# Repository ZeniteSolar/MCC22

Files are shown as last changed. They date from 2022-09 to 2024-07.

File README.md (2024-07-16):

# MCC22

## Build
```bash
cd firmware
make -j16 -f STM32Make.make
```

MPPT Battery charger

| Input Voltage | 0 ~ 30 V  |
| ---: | :--- |
| Output Voltage  | 21 ~ 60V  |
| Output Power | 300 W |
| Efficiency | > 90% |

## 3D Model

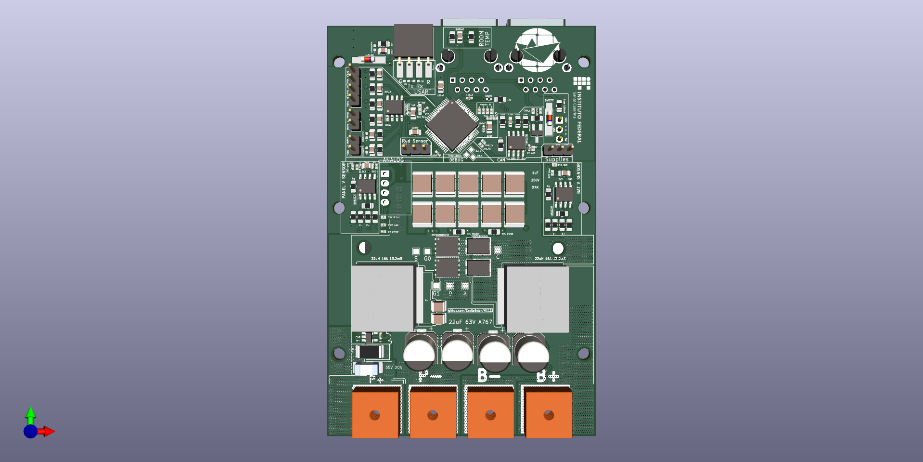
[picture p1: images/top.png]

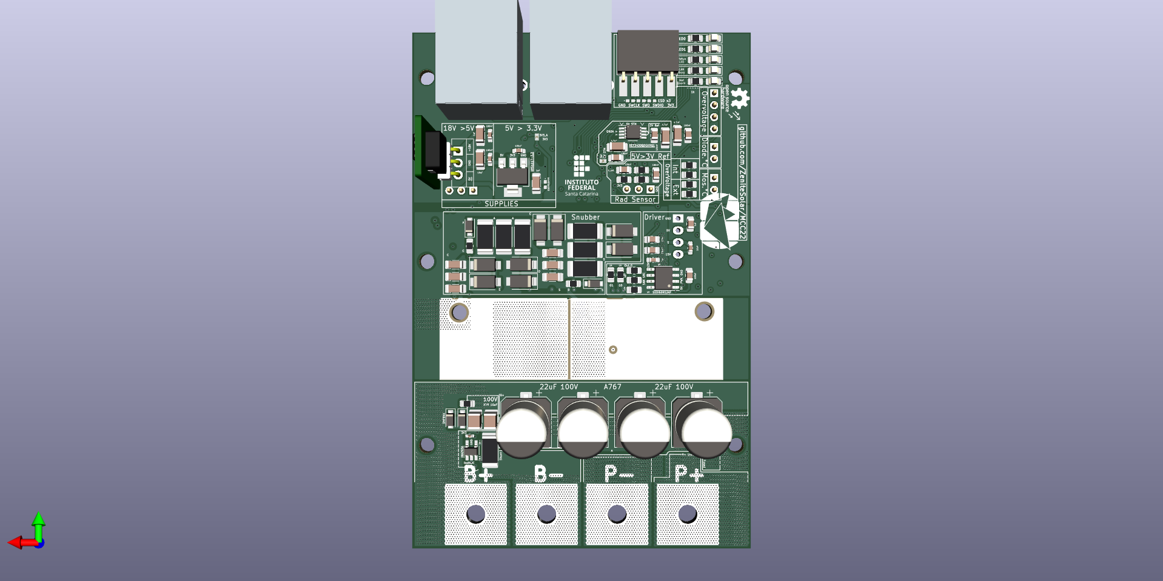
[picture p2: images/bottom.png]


## Soldered board

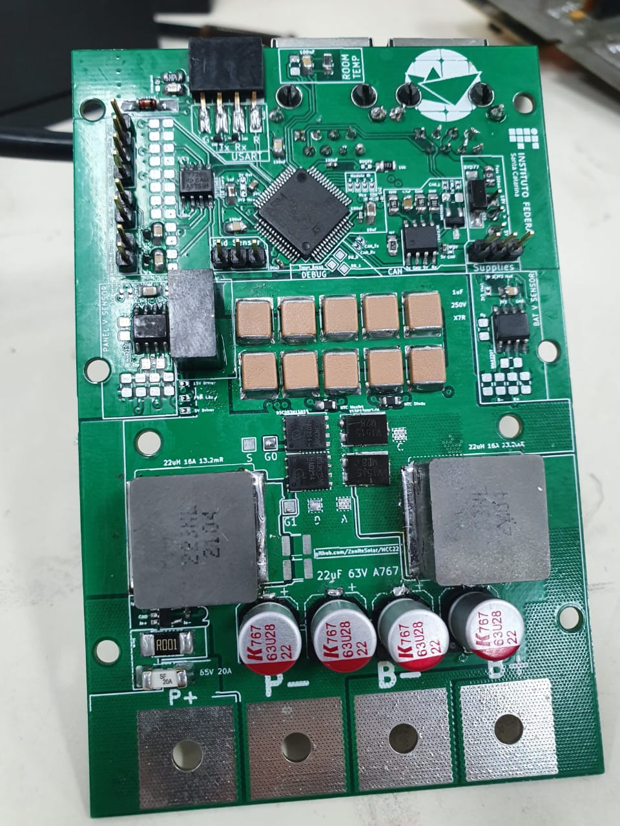
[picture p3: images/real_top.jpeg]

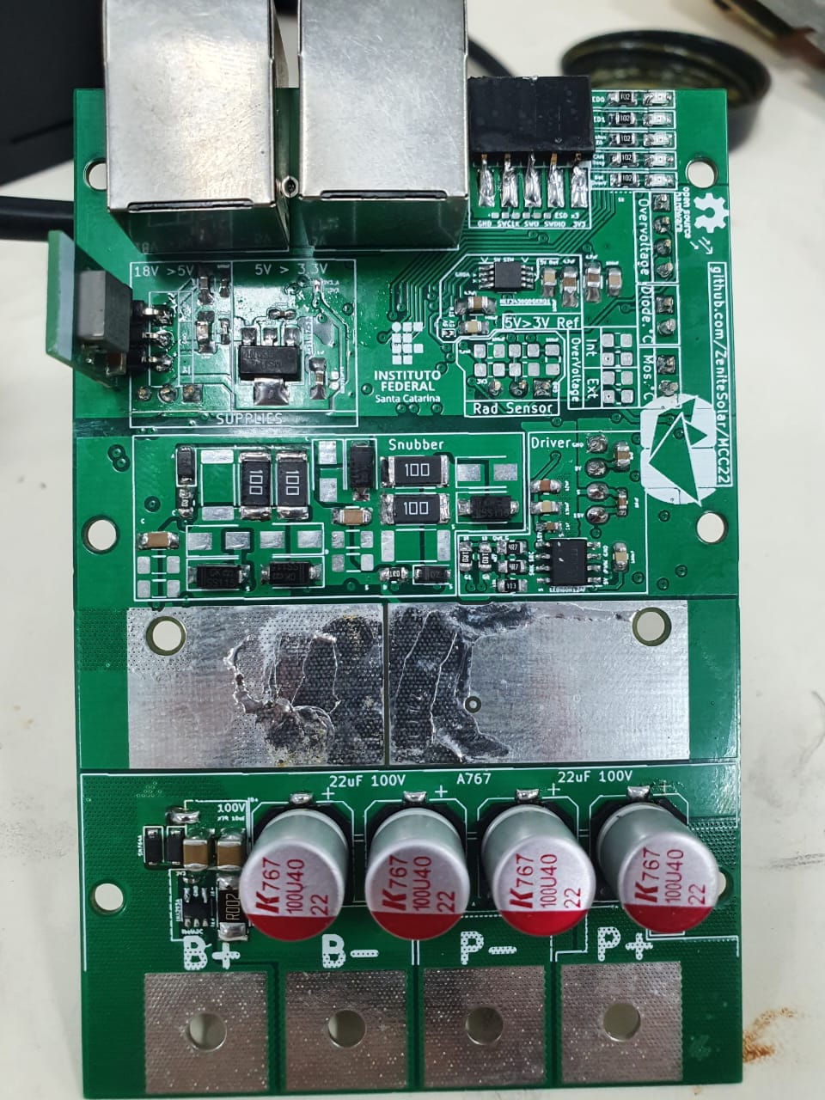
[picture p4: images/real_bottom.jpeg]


# Testing Guide for the MCC22 Board

Follow the steps below, if any value differs from the expected, abort the test. Power off and on after each step. Always limit the power source to 18V at 100mA. Use this [link](https://htmlpreview.github.io/?https://github.com/ZeniteSolar/MCC22/blob/main/hardware/main/bom/ibom.html) to find components on the board.

## Steps

1. Without any jumpers, connect the CAN with 18V, consumption should be approximately 1mA. On the power pin header (J601) there should be 5V and 3.3V at their respective pins.
2. Connect the STM 3.3V Enable jumper (JP101), consumption should be approximately 1mA.
3. Connect the STM32 Supply Enable jumper (JP201), consumption should be approximately 5mA. There should be 3.3V between the pins of capacitors C208 and C210.
4. Connect the STM 5V Enable jumper (JP103), consumption should be approximately 5mA. There should be 3V across the pins of capacitor C204.
5. Connect the Analog_Ref jumper (JP203) between the central pin and 3V_ref, consumption should be approximately 30mA. There should be 3V across the pins of capacitor C211.
6. Flash the STM32 (power should be on). When power is cycled, all LEDs should light up in sequence, excluding the Bat OverV LED. There should be a PWM signal on pin 1 of the PWM Enable jumper (JP106).
7. Connect the Enable_Analog jumper (JP102), the consumption should be approximately 5mA.
8. Connect a serial-USB converter and send the command `WRTE:SYST:PING?` to verify if UART is functioning, the response should be `PONG`.
9. Send the command `READ:MEAS:ALLM?`. After activating this flag, the board will continuously send the measurements it takes.
10. Connect a 10 Ohm resistor at the controller's output.
11. Send the command `WRTE:CTRL:ALGO:FIXD:0000.0000` to deactivate the PWM.
12. Connect the Disable_Vpanel jumper (JP301), the consumption should remain close to 5mA.
13. Connect the Disable_Vbat jumper (JP302), the consumption should remain close to 5mA.
14. Connect the Disable_Ibat jumper (JP304), the consumption should remain close to 5mA.
15. Connect the Disable_Ipanel jumper (JP303), the consumption should remain close to 5mA.
16. Connect a voltage source at P+ and P- with zero voltage and current at 10mA, increase the voltage to 30V and the VPan value on UART should follow the source voltage.
17. Connect a voltage source at B+ and B- with zero voltage and current at 10mA, increase the voltage to 60V and the Vbat value on UART should follow the source voltage.
18. Connect the Enable_Driver jumper (JP104) and consumption should be approximately 10mA. There should be 15V between pins 3 and 4 of the driver source (PS501).
19. Connect the Enable_Driver_5V jumper (JP502), Enable_Driver jumper (JP501), and Enable_PWM jumper (JP106), and the consumption should be approximately 12mA.
20. Send the command `WRTE:CTRL:ALGO:FIXD:0000.6000` to fix the PWM at 60%. Attach the oscilloscope's GND to test point S (TP404) **Other channels should have their GND disconnected!** and channel 1 to test point G0 (TP401). There should appear a square signal with a 60% duty cycle, same for G1 (TP402).
21. Connect a 10 Ohm load at the controller's output. Send the command `WRTE:CTRL:ALGO:FIXD:0000.6000`, connect a voltage source at P+ and P- with zero voltage and current at 1A, increase the voltage until the source limits and the Ipan value on UART should follow the source current.

Note: If any of the conditions are not met, there might be a potential issue with the board.

## Tests

All tests are in [this](./tests/tests.md) separated document.

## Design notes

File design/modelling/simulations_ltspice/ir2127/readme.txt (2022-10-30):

##########################################################################################
## Simulation model of IR2127 Level 1 for SIMetrix version 8.3g or higher
##########################################################################################

--------------------------------------------------------------------------------
1. Changelog
--------------------------------------------------------------------------------
VER    | BY                       | DATE          | OBS                         
--------------------------------------------------------------------------------
01.00  | GI                       | 2020-04-30    | created    (*1)
--------------------------------------------------------------------------------
01.01  | GI                       | 2020-12-02    | model update
--------------------------------------------------------------------------------
01.02  | GI                       | 2020-12-03    | model update
--------------------------------------------------------------------------------
01.03  | GI                       | 2020-12-04    | model update
--------------------------------------------------------------------------------

(*1) 
Simulation model of IR2127 Level 1 for SIMetrix version 8.3g or higher
Template performance : 
  - Static Electrical Characteristics and Dynamic Electrical Characteristics 
    are modeled with the typical values from the datasheet.
  - Temperature effects are not modeled
The following features have been modeled :
  - Switching Characteristics such as propagation delay, peak/mean currents
  - Undervoltage lockout 

--------------------------------------------------------------------------------
2. Supported platform
--------------------------------------------------------------------------------
This model has been successfully tested with the following software:
- SIMetrix 8.3g or newer versions

--------------------------------------------------------------------------------
3. Structure of the delivery package
--------------------------------------------------------------------------------
The delivery package contains the following:

	\Documentation\GettingStarted.pdf         : guidance on how to get started with the attached behavioral model
	\Documentation\Disclaimer.pdf             : Infineon’s model terms of use
	\Model\IR2127.lib                         : model lib file
	\Model\IR2127.sxslb                       : schematic symbol for the lib
	\Model\DEMO_TESTBENCH.sxsch               : demo testbench provided together with the model 
	\Model\IGBT_650V_TRENCHSTOP5_F5_L1.lib    : Infineon's IGBT model
	\Model\IGBT_650V_TRENCHSTOP5_F5_L1.sxslb  : Infineon's IGBT symbol for schematic
	\Model\results                            : some screenshots with the demo testbench and results
	
--------------------------------------------------------------------------------
4. Infineon contact and support
--------------------------------------------------------------------------------
support@infineon.com

--------------------------------------------------------------------------------
5. Disclaimer
--------------------------------------------------------------------------------

INFINEON’S MODEL TERMS OF USE

BY DOWNLOADING AND/OR USING THIS INFINEON MODEL (“MODEL”), THE USER (INCLUDING YOU) 
AGREES TO BE BOUND BY THE TERMS OF USE HERE STATED. IF USER DOES NOT AGREE TO ALL TERMS OF
USE HERE STATED, USER SHALL NOT DOWNLOAD, USE OR COPY THE MODEL BUT IMMEDIATELY DELETE 
IT (TO THE EXTENT THAT IT WAS DOWNLOADED ALREADY).

1. SCOPE OF USE
1.1 Any use of this Model provided by Infineon Technologies AG is subject to these Terms of Use.
1.2 This Model, provided by Infineon, does not fully represent all of the specifications and
operating characteristics of the product to which this Model relates.
1.3 This Model only describes the characteristics of a typical product. In all cases, the current data
sheet information for a given product is the final design guideline and the only actual 
performance specification. Although this Model can be a useful tool to evaluate the product 
performance, it cannot simulate the exact product performance under all conditions and it is 
also not intended to replace bread-boarding for final verification.

2. IMPORTANT NOTICE
2.1 Infineon Technologies AG (“Infineon”) is not and cannot be aware of the specific application of 
the Infineon’s Model by User. However, Model may from time to time be used by User in potentially 
harmful and/or life-endangering applications such as traffic, logistic, medical, nuclear or military a
pplications or in other applications where failure of the Model may predictably cause damage to 
persons’ life or health or to property (hereinafter "Critical Applications").
2.2 User acknowledges that Infineon has not specifically designed or qualified the Model for 
Critical Applications that the Model may contain errors and bugs and that User is required to 
qualify the Model for Critical Applications pursuant to the applicable local quality, safety and 
legal requirements before permitting or giving access to any such use.

3. CONFIDENTIAL INFORMATION
User shall treat ideas, concepts and information incorporated in the Model, the documentation and 
the content of this Terms of Use (together hereinafter "Confidential Information") confidential, not 
disclose it to any third party unless otherwise agreed in writing between User and Infineon, not use 
it for any other purposes than using the Model for simulation and testing purposes only.

4. WARRANTY
4.1 User acknowledges that the Model is provided by Infineon under this Terms of Use is provided free 
of charge and "AS IS" without any warranty or liability of any kind and Infineon hereby expressly 
disclaims any warranties or representations, whether express, implied, statutory or otherwise, 
including but not limited to warranties of workmanship, merchantability, fitness for a particular 
purpose, defects in the Model, or non-infringement of third parties intellectual property rights.
4.2 Infineon reserves the right to make corrections, deletions, modifications, enhancements, 
improvements and other changes to the Model at any time or to move or discontinue any Model without notice.

5. LIABILITY
5.1 Nothing in this Terms of Use shall limit or exclude Infineon's liability under mandatory liability 
laws, for injuries to life, body or health, for fraudulent concealment of defects in the software, or 
in cases of Infineon's intentional misconduct or gross negligence.
5.2 Without prejudice to Sections 5.1, in cases of Infineon's slight negligent breach of obligations 
that restrict essential rights or duties arising from the nature of this Terms of Use in a way that 
there is a risk of non-achievement of the purpose of this Terms of Use or of an obligation whose observance
User regularly may trust in and whereas compliance with only makes proper execution of this Terms 
of Use possible, Infineon's liability shall be limited to the typically, foreseeable damage.
5.3 Without prejudice to Sections 8.1 and 8.2, Infineon's liability under this Agreement shall be excluded in all 
other cases.

6. EXPORT REGULATIONS
The User shall comply with all applicable national and international laws and regulations, in 
particular the applicable export control regulations and sanction programs. The User also agrees 
not to export, re-export or transfer any software or technology developed with or using information, 
software or technology offered by Infineon, in violation of any applicable laws or regulations of 
the competent authorities. Further, the User shall neither use any products, information, software 
and technology offered by Infineon in or in connection with nuclear technology or weapons of mass 
destruction (nuclear, biological or chemical) and carriers thereof nor supply military consignees.

7. TERMINATION OF USE PERMIT
If the User violates these Terms of Use, such User’s permit to use this Model terminates automatically. 
In addition, Infineon may terminate the User’s permit to use this Model at its discretion and at 
any time regardless of any violation of these Terms of Use. In any of the foregoing events, the User 
is obliged to immediately destroy any content that has been downloaded or printed from Infineon’s website.

8. MISCELLANEOUS
8.1 These Terms of Use are subject to the laws of the Federal Republic of Germany with the exception 
of the United Nations on Purchase Contracts on the International Sale of Goods dated April 11, 1980 (CISG). 
The exclusive place of jurisdiction is Munich, Germany.
8.2 Should any provision in these Terms of Use be or become invalid, the validity of all other 
provisions or agreements shall remain unaffected thereby.

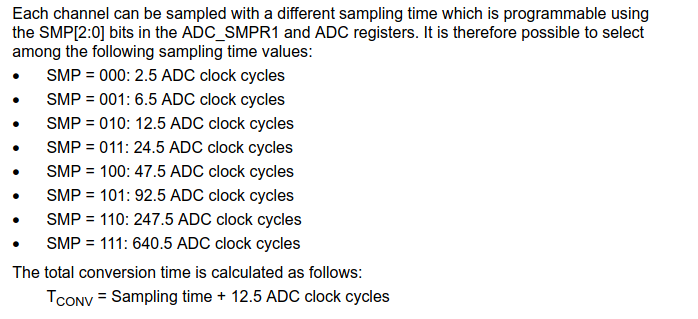
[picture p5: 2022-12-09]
design/img/Tsampl.png

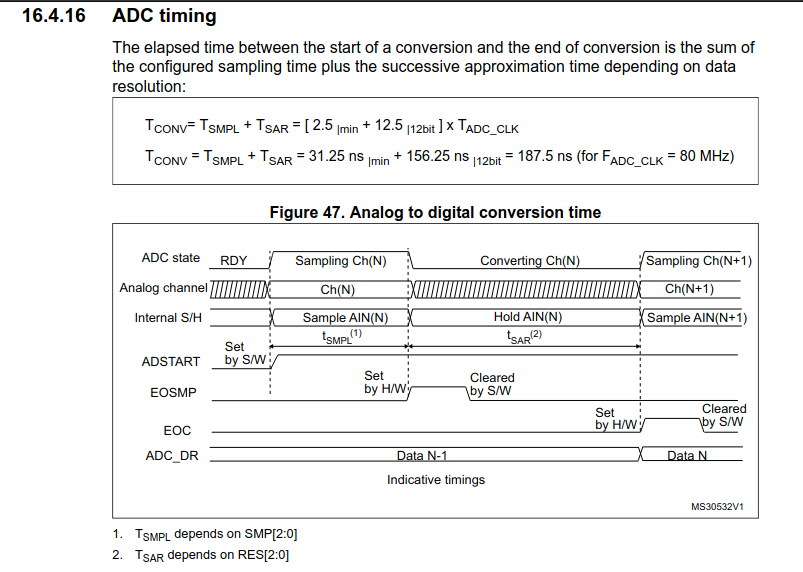
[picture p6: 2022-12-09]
design/img/ADC timing.png

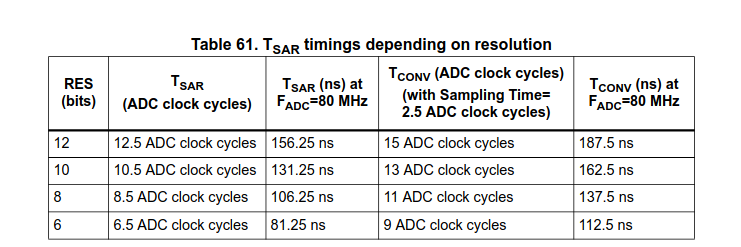
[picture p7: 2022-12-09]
design/img/Tsar.png

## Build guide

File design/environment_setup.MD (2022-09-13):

# Setting up the environment

### 1. Virtual Environment

```bash
python3.10 -m venv .venv
source .venv/bin/activate
python -m pip --upgrade pip
```

### 2. Project requirements
```bash
python -m pip install -r requirements.txt
```

Open `tllocalmgr` and:
```bash
install circuitikz
exit
```

and then:
```bash
sudo texhash
```

### 3.

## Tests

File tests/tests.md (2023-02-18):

### 1 Initial Test
The initial test of the system revealed that the inductor current was operating in a discontinuous mode, which resulted in poor efficiency and a significant amount of heat being generated in both the inductor and switches. After further analysis, two primary factors were identified.
- The first factor is the high ripple current in the inductor, which is causing increased core losses. 
- The second factor is the overly aggressive snubber, which is causing switching delays and high power dissipation in the snubber.

To explore the effects of different parameters on the system's performance, two tests were conducted using different switching frequencies of 40kHz and 100kHz. The duty cycle and load were varied to maintain a constant output voltage of 60V and input current levels of 3A and 6A. These tests were designed to identify the impact of these parameters on the system's efficiency, thermal behavior, and overall performance.

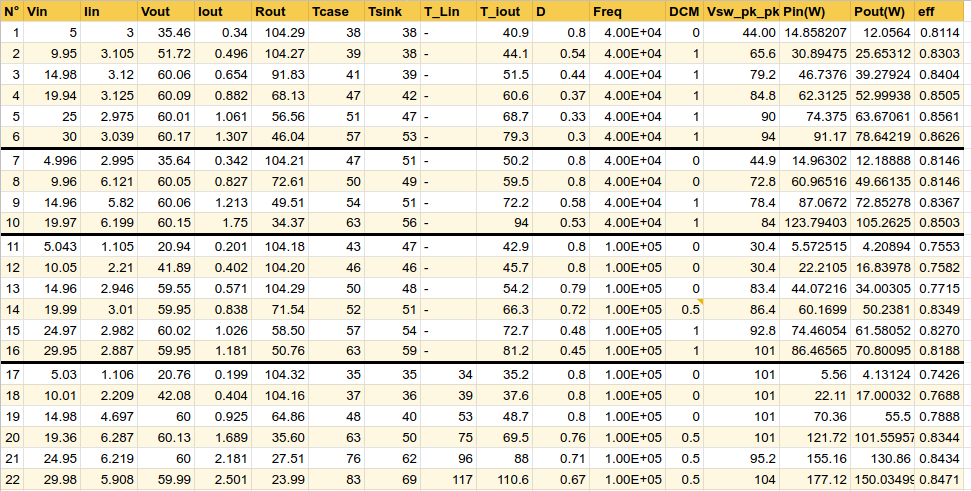
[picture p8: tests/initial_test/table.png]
table


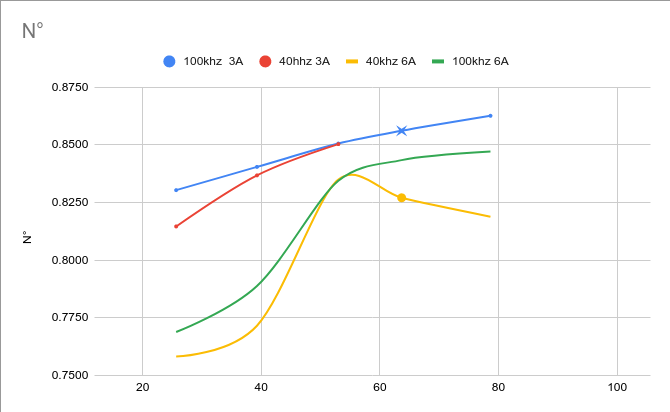
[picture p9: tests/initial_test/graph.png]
graph


### 2 Testing inductors

During the testing of the converter, it was observed that the inductor temperature exceeded 100º and it was in discontinuous mode. Was identified as the primary suspect for this issue the low inductance value of the current inductor, which was 100uH less than the previous design.

A test was conducted to compare the performance of the current inductor (22uH) comparing with the previous inductor (120uH). The test was performed under the same operating conditions with almost the same input power and output voltage.

table

**Inductor Current**
- Yellow: output inductor current.
- Blue: input inductor current.

<table>
    <tr>
        <td align="center">22uH</td>
        <td align="center">120uH</td>
    </tr>
    <tr>
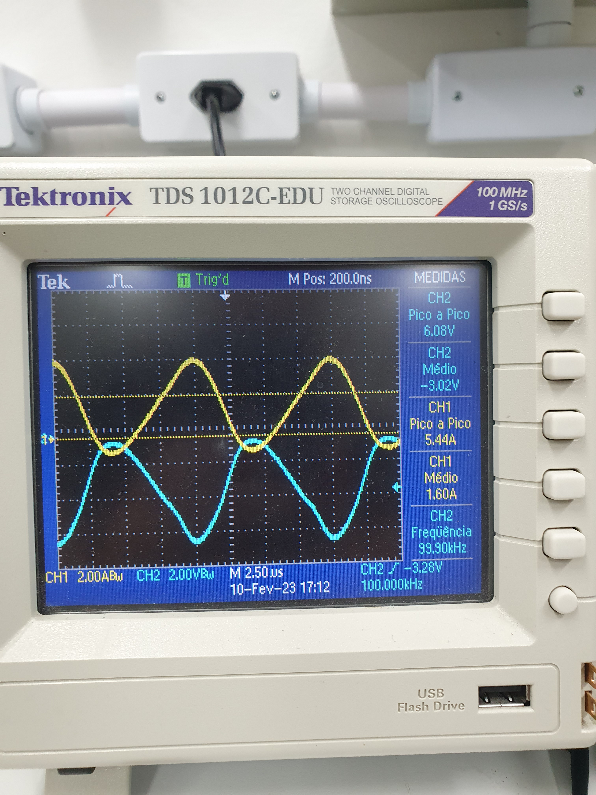
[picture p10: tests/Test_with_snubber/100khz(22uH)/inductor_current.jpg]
        <td></td>
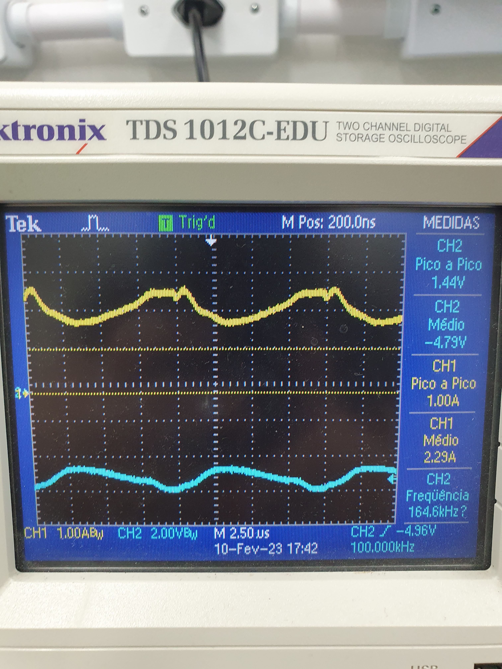
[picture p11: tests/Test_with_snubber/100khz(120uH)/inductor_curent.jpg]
        <td></td>
    </tr>
</table> 

**Switches Voltage**
- Yellow: Mosfet.
- Blue: Diode.

<table>
    <tr>
        <td align="center">22uH</td>
        <td align="center">120uH</td>
    </tr>
    <tr>
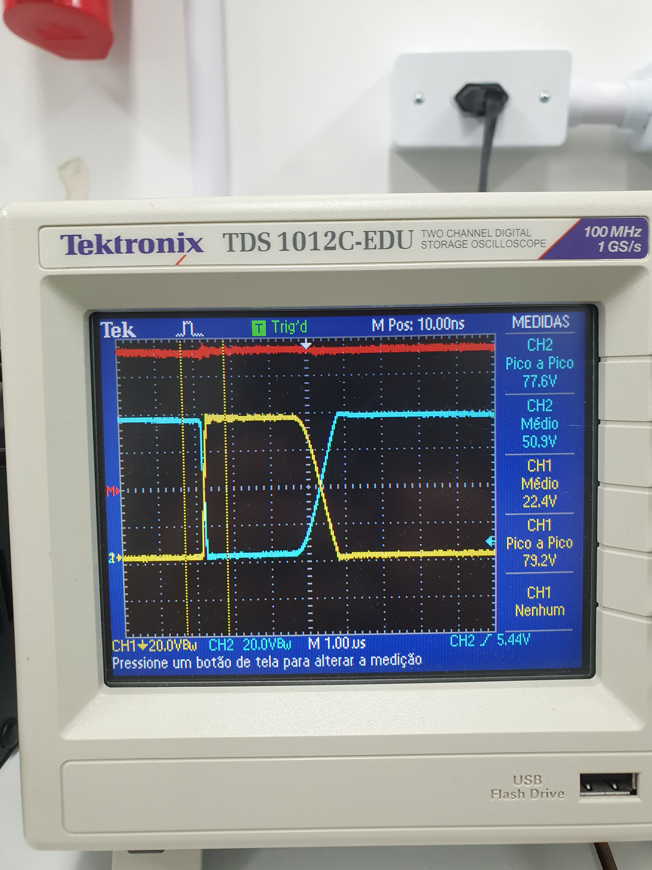
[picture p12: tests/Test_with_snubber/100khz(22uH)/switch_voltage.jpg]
        <td></td>
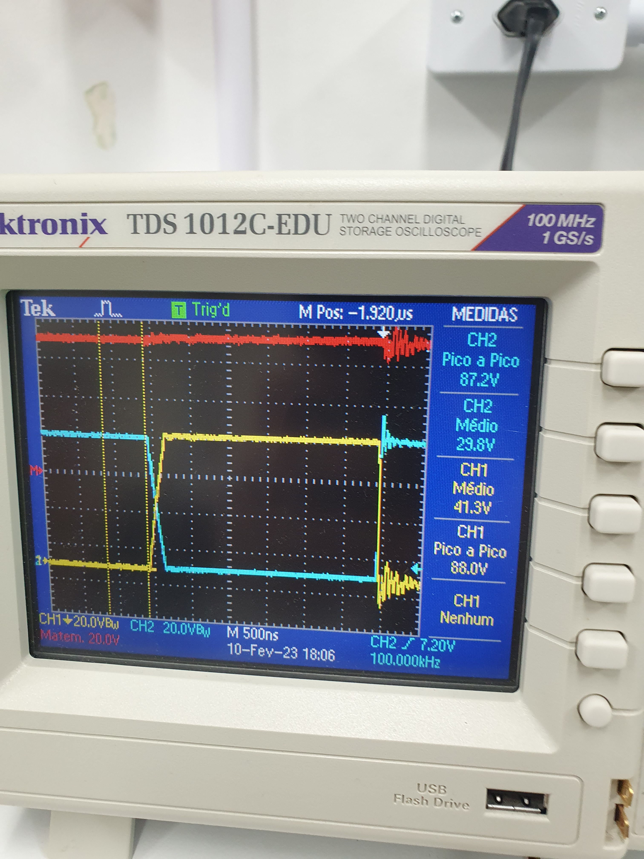
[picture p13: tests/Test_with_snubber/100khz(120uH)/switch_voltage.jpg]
        <td></td>
    </tr>
</table> 

After changing the inductor, it was observed that the converter's efficiency improved, although it did not meet the target efficiency of >90%. Increasing the operating frequency (above 100khz), reduced the inductor temperature. However, the temperature in the coupling capacitor area increased significantly, and the root cause of this issue could be attributed to either the coupling capacitor or the snubber.

### 3 Testing snubber losses

It was observed that as the frequency was increased, the temperature in the coupling capacitor and snubber area also increased. Despite this, the switches waveform remained smooth. To further investigate this phenomenon, the snubber was disconnected and the converter was subjected to a frequency range of 200kHz to 400kHz, using the 22uH inductor.

table

**Inductor Current**
- Yellow: output inductor current.
- Blue: input inductor current.

<table>
    <tr>
        <td align="center">200khz</td>
        <td align="center">300khz</td>
        <td align="center">400khz</td>
    </tr>
    <tr>
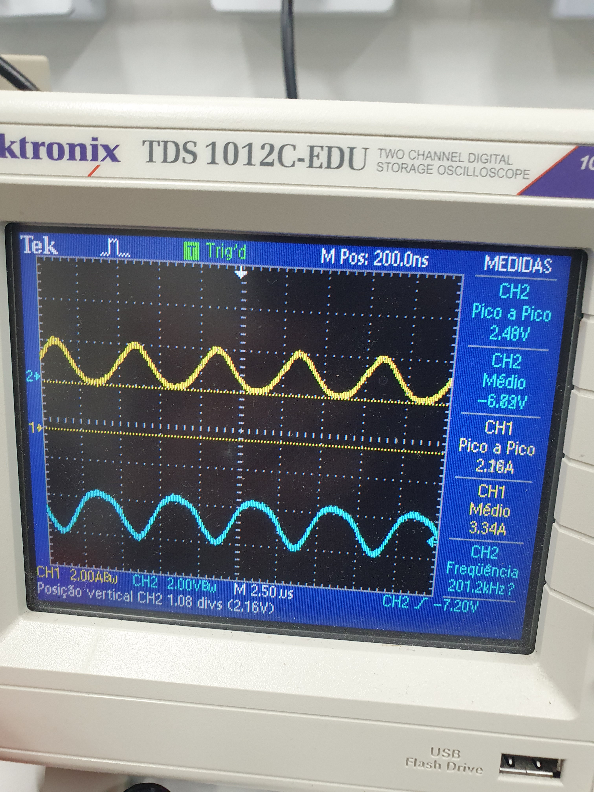
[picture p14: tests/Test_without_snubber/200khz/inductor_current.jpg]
        <td></td>
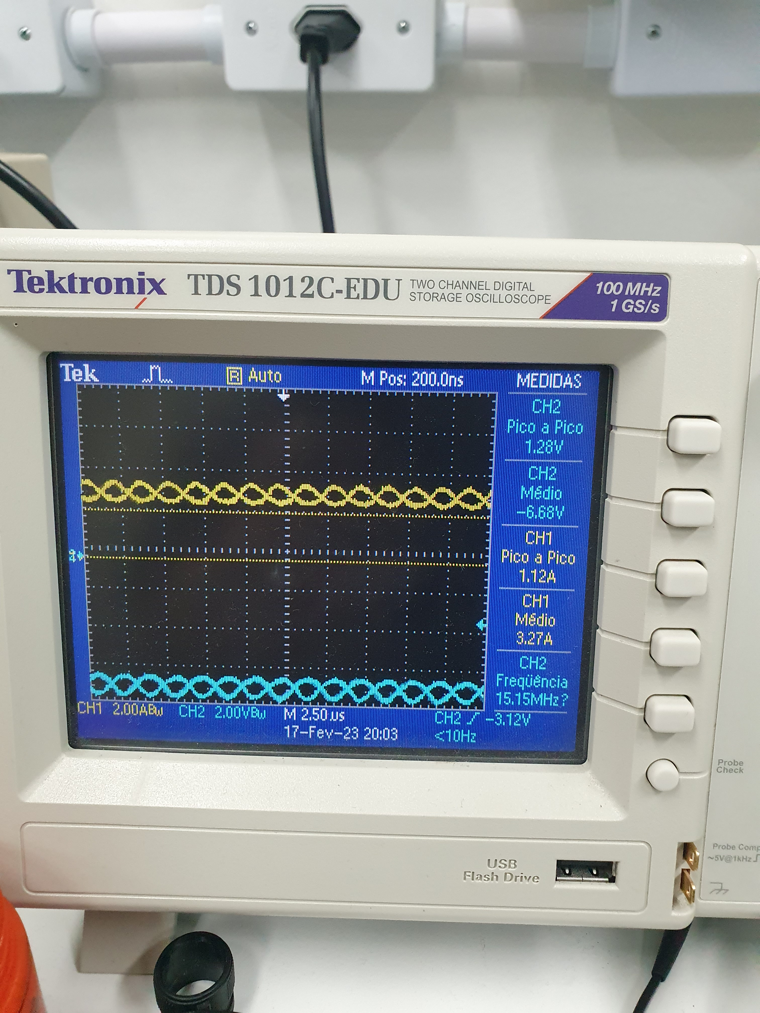
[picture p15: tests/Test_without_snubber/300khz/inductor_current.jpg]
        <td></td>
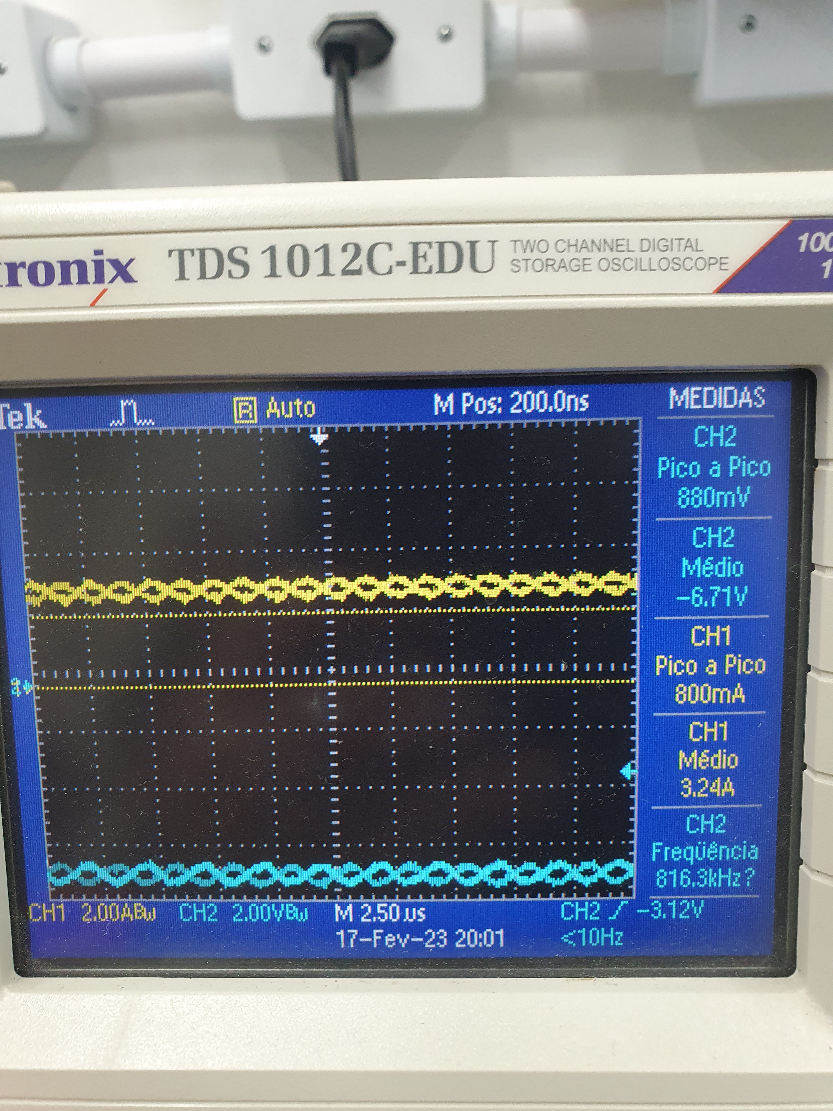
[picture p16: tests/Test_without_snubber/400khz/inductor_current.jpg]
        <td></td>
    </tr>
</table> 

**Switch Voltage**
- Yellow: Mosfet.
- Blue: Diode.

<table>
    <tr>
        <td align="center">200khz</td>
        <td align="center">300khz</td>
        <td align="center">400khz</td>
    </tr>
    <tr>
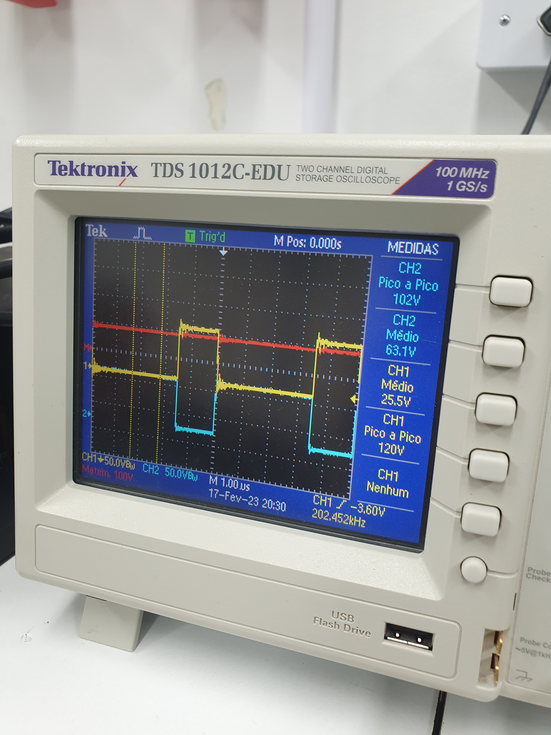
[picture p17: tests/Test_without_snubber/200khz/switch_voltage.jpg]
        <td></td>
        <td>graph</td>
        <td>graph</td>
    </tr>
</table> 

It was concluded that the snubber was responsible for the majority of losses, and the parasitic inductance was found to be quite low, because that the MOSFET voltage did not exceed 120V when the snubber was disconnected.

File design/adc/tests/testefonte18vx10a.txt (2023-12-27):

Algo: 0, Vpan: 18.49, Ipan: 3.69, Vbat: 0.00, Ibat: 0.00, Duty: 0.634, Freq: 300751.88, Pin: 68.30
Algo: 0, Vpan: 18.48, Ipan: 3.71, Vbat: 0.00, Ibat: 0.00, Duty: 0.634, Freq: 300751.88, Pin: 68.55
Algo: 0, Vpan: 18.38, Ipan: 3.93, Vbat: 0.00, Ibat: 0.00, Duty: 0.642, Freq: 300751.88, Pin: 72.24
Algo: 0, Vpan: 18.24, Ipan: 4.17, Vbat: 0.00, Ibat: 0.00, Duty: 0.649, Freq: 300751.88, Pin: 76.04
Algo: 0, Vpan: 18.25, Ipan: 4.17, Vbat: 0.00, Ibat: 0.00, Duty: 0.649, Freq: 300751.88, Pin: 76.02
Algo: 0, Vpan: 18.25, Ipan: 4.17, Vbat: 0.00, Ibat: 0.00, Duty: 0.649, Freq: 300751.88, Pin: 76.04
Setting gain of channel 2: 1.024000
busy
Setting gain of channel 2: 0.512000
busy
Setting gain of channel 2: 1.024000
busy
Algo: 0, Vpan: 18.38, Ipan: 3.93, Vbat: 0.00, Ibat: 0.00, Duty: 0.642, Freq: 300751.88, Pin: 72.23
Setting gain of channel 2: 0.512000
busy
Algo: 0, Vpan: 18.24, Ipan: 4.14, Vbat: 0.00, Ibat: 0.00, Duty: 0.649, Freq: 300751.88, Pin: 75.54
Algo: 0, Vpan: 18.25, Ipan: 4.17, Vbat: 0.00, Ibat: 0.00, Duty: 0.649, Freq: 300751.88, Pin: 76.01
Algo: 0, Vpan: 18.11, Ipan: 4.41, Vbat: 0.00, Ibat: 0.00, Duty: 0.657, Freq: 300751.88, Pin: 79.83
Setting gain of channel 0: 2.048000
busy
Algo: 0, Vpan: 17.93, Ipan: 4.65, Vbat: 0.00, Ibat: 0.00, Duty: 0.664, Freq: 300751.88, Pin: 83.44
Algo: 0, Vpan: 17.92, Ipan: 4.65, Vbat: 0.00, Ibat: 0.00, Duty: 0.664, Freq: 300751.88, Pin: 83.42
Algo: 0, Vpan: 17.92, Ipan: 4.65, Vbat: 0.00, Ibat: 0.00, Duty: 0.664, Freq: 300751.88, Pin: 83.38
Algo: 0, Vpan: 17.92, Ipan: 4.65, Vbat: 0.00, Ibat: 0.00, Duty: 0.664, Freq: 300751.88, Pin: 83.38
Algo: 0, Vpan: 17.73, Ipan: 4.91, Vbat: 0.00, Ibat: 0.00, Duty: 0.672, Freq: 300751.88, Pin: 87.08
Algo: 0, Vpan: 17.47, Ipan: 5.18, Vbat: 0.00, Ibat: 0.00, Duty: 0.679, Freq: 300751.88, Pin: 90.43
Algo: 0, Vpan: 17.48, Ipan: 5.17, Vbat: 0.00, Ibat: 0.00, Duty: 0.679, Freq: 300751.88, Pin: 90.43
Algo: 0, Vpan: 17.48, Ipan: 5.17, Vbat: 0.00, Ibat: 0.00, Duty: 0.679, Freq: 300751.88, Pin: 90.43
Algo: 0, Vpan: 17.69, Ipan: 4.91, Vbat: 0.00, Ibat: 0.00, Duty: 0.672, Freq: 300751.88, Pin: 86.84
Algo: 0, Vpan: 17.48, Ipan: 5.17, Vbat: 0.00, Ibat: 0.00, Duty: 0.679, Freq: 300751.88, Pin: 90.40
Setting gain of channel 2: 0.256000
busy
Algo: 0, Vpan: 17.47, Ipan: 5.18, Vbat: 0.00, Ibat: 0.00, Duty: 0.679, Freq: 300751.88, Pin: 90.43
Algo: 0, Vpan: 17.21, Ipan: 5.45, Vbat: 0.00, Ibat: 0.00, Duty: 0.687, Freq: 300751.88, Pin: 93.86
INFO: ==> STATE INITIALIZING
INFO: ==> STATE IDLE
Setting gain of channel 0: 2.048000
INFO: ==> STATE RUNNING
Setting gain of channel 1: 2.048000
busy
Setting gain of channel 2: 2.048000
busy
Setting gain of channel 3: 2.048000
Algo: 2, Vpan: 20.03, Ipan: 0.05, Vbat: 0.00, Ibat: 0.00, Duty: 0.000, Freq: 300751.88, Pin: 1.04
Setting gain of channel 0: 1.024000
busy
Setting gain of channel 2: 1.024000
busy
Setting gain of channel 2: 0.512000
busy
Algo: 2, Vpan: 18.58, Ipan: 2.64, Vbat: 0.00, Ibat: 0.00, Duty: 0.627, Freq: 300751.88, Pin: 49.04
Setting gain of channel 2: 0.256000
busy
Algo: 2, Vpan: 18.24, Ipan: 4.42, Vbat: 0.00, Ibat: 0.00, Duty: 0.657, Freq: 300751.88, Pin: 80.57
Setting gain of channel 0: 2.048000
busy
Algo: 2, Vpan: 17.26, Ipan: 5.02, Vbat: 0.00, Ibat: 0.00, Duty: 0.687, Freq: 300751.88, Pin: 86.75
Algo: 2, Vpan: 16.06, Ipan: 6.73, Vbat: 0.00, Ibat: 0.00, Duty: 0.716, Freq: 300751.88, Pin: 108.11
Setting gain of channel 2: 0.512000
busy
Setting gain of channel 2: 0.256000
busy
Algo: 2, Vpan: 14.36, Ipan: 8.07, Vbat: 0.00, Ibat: 0.00, Duty: 0.746, Freq: 300751.88, Pin: 115.84
Setting gain of channel 2: 0.512000
busy
Algo: 2, Vpan: 11.07, Ipan: 8.01, Vbat: 0.00, Ibat: 0.00, Duty: 0.776, Freq: 300751.88, Pin: 88.70
Setting gain of channel 1: 1.024000
busy
Algo: 2, Vpan: 8.22, Ipan: 8.15, Vbat: 0.00, Ibat: 0.00, Duty: 0.799, Freq: 300751.88, Pin: 66.97
Setting gain of channel 1: 2.048000
busy
Algo: 2, Vpan: 10.87, Ipan: 7.86, Vbat: 0.00, Ibat: 0.00, Duty: 0.769, Freq: 300751.88, Pin: 85.50
Setting gain of channel 2: 0.256000
busy
Brute force done!
Algo: 2, Vpan: 14.07, Ipan: 7.39, Vbat: 0.00, Ibat: 0.00, Duty: 0.739, Freq: 300751.88, Pin: 104.00
Setting gain of channel 2: 0.512000
busy
Setting gain of channel 2: 0.256000
Algo: 0, Vpan: 14.09, Ipan: 7.39, Vbat: 0.00, Ibat: 0.00, Duty: 0.739, Freq: 300751.88, Pin: 104.19
Algo: 0, Vpan: 13.18, Ipan: 7.54, Vbat: 0.00, Ibat: 0.00, Duty: 0.746, Freq: 300751.88, Pin: 99.42
Algo: 0, Vpan: 13.17, Ipan: 7.54, Vbat: 0.00, Ibat: 0.00, Duty: 0.746, Freq: 300751.88, Pin: 99.31
Algo: 0, Vpan: 13.16, Ipan: 7.53, Vbat: 0.00, Ibat: 0.00, Duty: 0.746, Freq: 300751.88, Pin: 99.12
Algo: 0, Vpan: 13.15, Ipan: 7.52, Vbat: 0.00, Ibat: 0.00, Duty: 0.746, Freq: 300751.88, Pin: 98.96
Algo: 0, Vpan: 13.15, Ipan: 7.52, Vbat: 0.00, Ibat: 0.00, Duty: 0.746, Freq: 300751.88, Pin: 98.86
Algo: 0, Vpan: 13.15, Ipan: 7.51, Vbat: 0.00, Ibat: 0.00, Duty: 0.746, Freq: 300751.88, Pin: 98.76
Algo: 0, Vpan: 13.14, Ipan: 7.51, Vbat: 0.00, Ibat: 0.00, Duty: 0.746, Freq: 300751.88, Pin: 98.62
Algo: 0, Vpan: 13.14, Ipan: 7.51, Vbat: 0.00, Ibat: 0.00, Duty: 0.746, Freq: 300751.88, Pin: 98.69
Setting gain of channel 2: 0.512000
busy
Algo: 0, Vpan: 14.04, Ipan: 7.36, Vbat: 0.00, Ibat: 0.00, Duty: 0.739, Freq: 300751.88, Pin: 103.39
Setting gain of channel 2: 0.256000
busy
Setting gain of channel 2: 0.512000
busy
Setting gain of channel 2: 0.256000
busy
Algo: 0, Vpan: 14.83, Ipan: 7.23, Vbat: 0.00, Ibat: 0.00, Duty: 0.731, Freq: 300751.88, Pin: 107.22
Setting gain of channel 2: 0.512000
busy
Setting gain of channel 2: 0.256000
busy
Setting gain of channel 2: 0.512000
busy
Algo: 0, Vpan: 15.66, Ipan: 7.09, Vbat: 0.00, Ibat: 0.00, Duty: 0.724, Freq: 300751.88, Pin: 111.00
Setting gain of channel 2: 0.256000
busy
Setting gain of channel 2: 0.512000
busy
Setting gain of channel 2: 0.256000
busy
Algo: 0, Vpan: 15.66, Ipan: 7.07, Vbat: 0.00, Ibat: 0.00, Duty: 0.724, Freq: 300751.88, Pin: 110.80
Algo: 0, Vpan: 15.66, Ipan: 7.07, Vbat: 0.00, Ibat: 0.00, Duty: 0.724, Freq: 300751.88, Pin: 110.82
Algo: 0, Vpan: 14.93, Ipan: 7.24, Vbat: 0.00, Ibat: 0.00, Duty: 0.731, Freq: 300751.88, Pin: 108.05
Algo: 0, Vpan: 15.66, Ipan: 7.07, Vbat: 0.00, Ibat: 0.00, Duty: 0.724, Freq: 300751.88, Pin: 110.79
Algo: 0, Vpan: 15.66, Ipan: 7.07, Vbat: 0.00, Ibat: 0.00, Duty: 0.724, Freq: 300751.88, Pin: 110.80
Setting gain of channel 2: 0.512000
busy
Setting gain of channel 2: 0.256000
busy
Algo: 0, Vpan: 16.05, Ipan: 6.75, Vbat: 0.00, Ibat: 0.00, Duty: 0.716, Freq: 300751.88, Pin: 108.32
Setting gain of channel 2: 0.512000
busy
Setting gain of channel 2: 0.256000
busy
Algo: 0, Vpan: 15.67, Ipan: 7.07, Vbat: 0.00, Ibat: 0.00, Duty: 0.724, Freq: 300751.88, Pin: 110.80
Algo: 0, Vpan: 15.67, Ipan: 7.07, Vbat: 0.00, Ibat: 0.00, Duty: 0.724, Freq: 300751.88, Pin: 110.81
Algo: 0, Vpan: 15.26, Ipan: 7.43, Vbat: 0.00, Ibat: 0.00, Duty: 0.731, Freq: 300751.88, Pin: 113.37
Algo: 0, Vpan: 14.08, Ipan: 7.38, Vbat: 0.00, Ibat: 0.00, Duty: 0.739, Freq: 300751.88, Pin: 103.88
Algo: 0, Vpan: 14.78, Ipan: 7.23, Vbat: 0.00, Ibat: 0.00, Duty: 0.731, Freq: 300751.88, Pin: 106.80
Algo: 0, Vpan: 15.65, Ipan: 7.06, Vbat: 0.00, Ibat: 0.00, Duty: 0.724, Freq: 300751.88, Pin: 110.53
Setting gain of channel 2: 0.512000
busy
Setting gain of channel 2: 0.256000
Algo: 0, Vpan: 15.65, Ipan: 7.06, Vbat: 0.00, Ibat: 0.00, Duty: 0.724, Freq: 300751.88, Pin: 110.46
Setting gain of channel 2: 0.512000
busy
Setting gain of channel 2: 0.256000
busy
Algo: 0, Vpan: 15.65, Ipan: 7.06, Vbat: 0.00, Ibat: 0.00, Duty: 0.724, Freq: 300751.88, Pin: 110.47
Setting gain of channel 2: 0.512000
busy
Setting gain of channel 2: 0.256000
busy
Algo: 0, Vpan: 14.92, Ipan: 7.27, Vbat: 0.00, Ibat: 0.00, Duty: 0.731, Freq: 300751.88, Pin: 108.38
Algo: 0, Vpan: 15.58, Ipan: 7.06, Vbat: 0.00, Ibat: 0.00, Duty: 0.724, Freq: 300751.88, Pin: 109.94
Algo: 0, Vpan: 15.65, Ipan: 7.06, Vbat: 0.00, Ibat: 0.00, Duty: 0.724, Freq: 300751.88, Pin: 110.44
Algo: 0, Vpan: 16.03, Ipan: 6.70, Vbat: 0.00, Ibat: 0.00, Duty: 0.716, Freq: 300751.88, Pin: 107.37
Setting gain of channel 2: 0.512000
busy
Algo: 0, Vpan: 15.65, Ipan: 7.02, Vbat: 0.00, Ibat: 0.00, Duty: 0.724, Freq: 300751.88, Pin: 109.87
Setting gain of channel 2: 0.256000
busy
Setting gain of channel 2: 0.512000
busy
Setting gain of channel 2: 0.256000
busy
Setting gain of channel 2: 0.512000
busy
Algo: 0, Vpan: 15.65, Ipan: 7.06, Vbat: 0.00, Ibat: 0.00, Duty: 0.724, Freq: 300751.88, Pin: 110.42
Setting gain of channel 2: 0.256000
busy
Algo: 0, Vpan: 15.58, Ipan: 7.58, Vbat: 0.00, Ibat: 0.00, Duty: 0.731, Freq: 300751.88, Pin: 118.07
Algo: 0, Vpan: 15.68, Ipan: 8.22, Vbat: 0.00, Ibat: 0.00, Duty: 0.739, Freq: 300751.88, Pin: 128.83
Setting gain of channel 2: 0.512000
busy
Setting gain of channel 2: 0.256000
busy
Algo: 0, Vpan: 15.37, Ipan: 8.78, Vbat: 0.00, Ibat: 0.00, Duty: 0.746, Freq: 300751.88, Pin: 134.87
Algo: 0, Vpan: 15.37, Ipan: 8.78, Vbat: 0.00, Ibat: 0.00, Duty: 0.746, Freq: 300751.88, Pin: 134.84
Algo: 0, Vpan: 15.37, Ipan: 8.77, Vbat: 0.00, Ibat: 0.00, Duty: 0.746, Freq: 300751.88, Pin: 134.79
Algo: 0, Vpan: 15.37, Ipan: 8.77, Vbat: 0.00, Ibat: 0.00, Duty: 0.746, Freq: 300751.88, Pin: 134.79
Algo: 0, Vpan: 15.08, Ipan: 9.13, Vbat: 0.00, Ibat: 0.00, Duty: 0.754, Freq: 300751.88, Pin: 137.66
Setting gain of channel 0: 4.096000
busy
Algo: 0, Vpan: 14.51, Ipan: 9.50, Vbat: 0.00, Ibat: 0.00, Duty: 0.761, Freq: 300751.88, Pin: 137.85
Setting gain of channel 2: 0.512000
busy
Setting gain of channel 2: 0.256000
busy
Algo: 0, Vpan: 14.41, Ipan: 9.50, Vbat: 0.00, Ibat: 0.00, Duty: 0.761, Freq: 300751.88, Pin: 136.94
Algo: 0, Vpan: 14.41, Ipan: 9.50, Vbat: 0.00, Ibat: 0.00, Duty: 0.761, Freq: 300751.88, Pin: 136.86
Algo: 0, Vpan: 14.40, Ipan: 9.50, Vbat: 0.00, Ibat: 0.00, Duty: 0.761, Freq: 300751.88, Pin: 136.83
Algo: 0, Vpan: 14.40, Ipan: 9.49, Vbat: 0.00, Ibat: 0.00, Duty: 0.761, Freq: 300751.88, Pin: 136.72
Algo: 0, Vpan: 14.40, Ipan: 9.49, Vbat: 0.00, Ibat: 0.00, Duty: 0.761, Freq: 300751.88, Pin: 136.72
Setting gain of channel 2: 0.512000
busy
Algo: 0, Vpan: 13.84, Ipan: 9.85, Vbat: 0.00, Ibat: 0.00, Duty: 0.769, Freq: 300751.88, Pin: 136.33
Setting gain of channel 2: 0.256000
busy
Setting gain of channel 2: 0.512000
busy
Setting gain of channel 2: 0.256000
busy
Algo: 0, Vpan: 14.40, Ipan: 9.53, Vbat: 0.00, Ibat: 0.00, Duty: 0.761, Freq: 300751.88, Pin: 137.17
Algo: 0, Vpan: 14.40, Ipan: 9.48, Vbat: 0.00, Ibat: 0.00, Duty: 0.761, Freq: 300751.88, Pin: 136.53
Algo: 0, Vpan: 14.39, Ipan: 9.49, Vbat: 0.00, Ibat: 0.00, Duty: 0.761, Freq: 300751.88, Pin: 136.54
Algo: 0, Vpan: 13.84, Ipan: 9.85, Vbat: 0.00, Ibat: 0.00, Duty: 0.769, Freq: 300751.88, Pin: 136.24
Setting gain of channel 2: 0.512000
busy
Setting gain of channel 2: 0.256000
busy
Algo: 0, Vpan: 14.34, Ipan: 9.49, Vbat: 0.00, Ibat: 0.00, Duty: 0.761, Freq: 300751.88, Pin: 136.02
Algo: 0, Vpan: 13.83, Ipan: 9.84, Vbat: 0.00, Ibat: 0.00, Duty: 0.769, Freq: 300751.88, Pin: 136.14
Algo: 0, Vpan: 13.30, Ipan: 10.27, Vbat: 0.00, Ibat: 0.00, Duty: 0.776, Freq: 300751.88, Pin: 136.59
Algo: 0, Vpan: 14.39, Ipan: 9.48, Vbat: 0.00, Ibat: 0.00, Duty: 0.761, Freq: 300751.88, Pin: 136.37
Setting gain of channel 0: 2.048000
busy
Algo: 0, Vpan: 14.95, Ipan: 9.07, Vbat: 0.00, Ibat: 0.00, Duty: 0.754, Freq: 300751.88, Pin: 135.59
Setting gain of channel 0: 4.096000
busy
Setting gain of channel 2: 0.512000
busy
Algo: 0, Vpan: 14.39, Ipan: 9.48, Vbat: 0.00, Ibat: 0.00, Duty: 0.761, Freq: 300751.88, Pin: 136.43
Setting gain of channel 2: 0.256000
busy
Algo: 0, Vpan: 13.83, Ipan: 9.87, Vbat: 0.00, Ibat: 0.00, Duty: 0.769, Freq: 300751.88, Pin: 136.54
Algo: 0, Vpan: 13.83, Ipan: 9.86, Vbat: 0.00, Ibat: 0.00, Duty: 0.769, Freq: 300751.88, Pin: 136.40
Algo: 0, Vpan: 13.82, Ipan: 9.87, Vbat: 0.00, Ibat: 0.00, Duty: 0.769, Freq: 300751.88, Pin: 136.41
Algo: 0, Vpan: 14.39, Ipan: 9.50, Vbat: 0.00, Ibat: 0.00, Duty: 0.761, Freq: 300751.88, Pin: 136.74
Setting gain of channel 0: 2.048000
busy
Algo: 0, Vpan: 14.89, Ipan: 9.06, Vbat: 0.00, Ibat: 0.00, Duty: 0.754, Freq: 300751.88, Pin: 134.93
Setting gain of channel 0: 4.096000
busy
Algo: 0, Vpan: 14.45, Ipan: 9.47, Vbat: 0.00, Ibat: 0.00, Duty: 0.761, Freq: 300751.88, Pin: 136.81
Algo: 0, Vpan: 13.88, Ipan: 9.86, Vbat: 0.00, Ibat: 0.00, Duty: 0.769, Freq: 300751.88, Pin: 136.82
Algo: 0, Vpan: 13.82, Ipan: 9.86, Vbat: 0.00, Ibat: 0.00, Duty: 0.769, Freq: 300751.88, Pin: 136.26
Algo: 0, Vpan: 13.82, Ipan: 9.85, Vbat: 0.00, Ibat: 0.00, Duty: 0.769, Freq: 300751.88, Pin: 136.17
Algo: 0, Vpan: 13.82, Ipan: 9.85, Vbat: 0.00, Ibat: 0.00, Duty: 0.769, Freq: 300751.88, Pin: 136.10
Algo: 0, Vpan: 13.82, Ipan: 9.85, Vbat: 0.00, Ibat: 0.00, Duty: 0.769, Freq: 300751.88, Pin: 136.14
Algo: 0, Vpan: 14.38, Ipan: 9.45, Vbat: 0.00, Ibat: 0.00, Duty: 0.761, Freq: 300751.88, Pin: 135.91
Algo: 0, Vpan: 13.82, Ipan: 9.84, Vbat: 0.00, Ibat: 0.00, Duty: 0.769, Freq: 300751.88, Pin: 136.02
Algo: 0, Vpan: 13.81, Ipan: 9.85, Vbat: 0.00, Ibat: 0.00, Duty: 0.769, Freq: 300751.88, Pin: 136.01
Setting gain of channel 2: 0.512000
busy
Algo: 0, Vpan: 13.82, Ipan: 9.84, Vbat: 0.00, Ibat: 0.00, Duty: 0.769, Freq: 300751.88, Pin: 135.98
Algo: 0, Vpan: 13.81, Ipan: 9.84, Vbat: 0.00, Ibat: 0.00, Duty: 0.769, Freq: 300751.88, Pin: 135.91
Algo: 0, Vpan: 13.81, Ipan: 9.84, Vbat: 0.00, Ibat: 0.00, Duty: 0.769, Freq: 300751.88, Pin: 135.89
Algo: 0, Vpan: 13.81, Ipan: 9.84, Vbat: 0.00, Ibat: 0.00, Duty: 0.769, Freq: 300751.88, Pin: 135.85
Algo: 0, Vpan: 13.81, Ipan: 9.83, Vbat: 0.00, Ibat: 0.00, Duty: 0.769, Freq: 300751.88, Pin: 135.75
Algo: 0, Vpan: 13.81, Ipan: 9.83, Vbat: 0.00, Ibat: 0.00, Duty: 0.769, Freq: 300751.88, Pin: 135.74
Algo: 0, Vpan: 13.81, Ipan: 9.83, Vbat: 0.00, Ibat: 0.00, Duty: 0.769, Freq: 300751.88, Pin: 135.73
Algo: 0, Vpan: 13.81, Ipan: 9.83, Vbat: 0.00, Ibat: 0.00, Duty: 0.769, Freq: 300751.88, Pin: 135.68
Algo: 0, Vpan: 13.81, Ipan: 9.82, Vbat: 0.00, Ibat: 0.00, Duty: 0.769, Freq: 300751.88, Pin: 135.61
Algo: 0, Vpan: 13.80, Ipan: 9.83, Vbat: 0.00, Ibat: 0.00, Duty: 0.769, Freq: 300751.88, Pin: 135.65
Algo: 0, Vpan: 13.22, Ipan: 10.21, Vbat: 0.00, Ibat: 0.00, Duty: 0.776, Freq: 300751.88, Pin: 134.99
Algo: 0, Vpan: 13.80, Ipan: 9.82, Vbat: 0.00, Ibat: 0.00, Duty: 0.769, Freq: 300751.88, Pin: 135.55
Algo: 0, Vpan: 13.80, Ipan: 9.82, Vbat: 0.00, Ibat: 0.00, Duty: 0.769, Freq: 300751.88, Pin: 135.54
Algo: 0, Vpan: 13.80, Ipan: 9.82, Vbat: 0.00, Ibat: 0.00, Duty: 0.769, Freq: 300751.88, Pin: 135.47
Algo: 0, Vpan: 13.80, Ipan: 9.82, Vbat: 0.00, Ibat: 0.00, Duty: 0.769, Freq: 300751.88, Pin: 135.49
Algo: 0, Vpan: 14.37, Ipan: 9.42, Vbat: 0.00, Ibat: 0.00, Duty: 0.761, Freq: 300751.88, Pin: 135.37
Algo: 0, Vpan: 13.80, Ipan: 9.78, Vbat: 0.00, Ibat: 0.00, Duty: 0.769, Freq: 300751.88, Pin: 134.96
Algo: 0, Vpan: 14.32, Ipan: 9.42, Vbat: 0.00, Ibat: 0.00, Duty: 0.761, Freq: 300751.88, Pin: 134.90
Algo: 0, Vpan: 13.80, Ipan: 9.81, Vbat: 0.00, Ibat: 0.00, Duty: 0.769, Freq: 300751.88, Pin: 135.36
Algo: 0, Vpan: 13.80, Ipan: 9.80, Vbat: 0.00, Ibat: 0.00, Duty: 0.769, Freq: 300751.88, Pin: 135.28
Algo: 0, Vpan: 13.80, Ipan: 9.81, Vbat: 0.00, Ibat: 0.00, Duty: 0.769, Freq: 300751.88, Pin: 135.31
Algo: 0, Vpan: 14.32, Ipan: 9.41, Vbat: 0.00, Ibat: 0.00, Duty: 0.761, Freq: 300751.88, Pin: 134.79
Algo: 0, Vpan: 13.80, Ipan: 9.80, Vbat: 0.00, Ibat: 0.00, Duty: 0.769, Freq: 300751.88, Pin: 135.29
Algo: 0, Vpan: 13.80, Ipan: 9.80, Vbat: 0.00, Ibat: 0.00, Duty: 0.769, Freq: 300751.88, Pin: 135.26
Algo: 0, Vpan: 13.80, Ipan: 9.80, Vbat: 0.00, Ibat: 0.00, Duty: 0.769, Freq: 300751.88, Pin: 135.24
Algo: 0, Vpan: 13.80, Ipan: 9.80, Vbat: 0.00, Ibat: 0.00, Duty: 0.769, Freq: 300751.88, Pin: 135.17
Algo: 0, Vpan: 13.80, Ipan: 9.79, Vbat: 0.00, Ibat: 0.00, Duty: 0.769, Freq: 300751.88, Pin: 135.10
Algo: 0, Vpan: 13.79, Ipan: 9.79, Vbat: 0.00, Ibat: 0.00, Duty: 0.769, Freq: 300751.88, Pin: 135.00
Algo: 0, Vpan: 13.79, Ipan: 9.79, Vbat: 0.00, Ibat: 0.00, Duty: 0.769, Freq: 300751.88, Pin: 134.91
Algo: 0, Vpan: 13.79, Ipan: 9.79, Vbat: 0.00, Ibat: 0.00, Duty: 0.769, Freq: 300751.88, Pin: 135.01
Algo: 0, Vpan: 13.21, Ipan: 10.18, Vbat: 0.00, Ibat: 0.00, Duty: 0.776, Freq: 300751.88, Pin: 134.39
Algo: 0, Vpan: 13.79, Ipan: 9.79, Vbat: 0.00, Ibat: 0.00, Duty: 0.769, Freq: 300751.88, Pin: 134.97
Algo: 0, Vpan: 13.79, Ipan: 9.78, Vbat: 0.00, Ibat: 0.00, Duty: 0.769, Freq: 300751.88, Pin: 134.97
Algo: 0, Vpan: 13.79, Ipan: 9.79, Vbat: 0.00, Ibat: 0.00, Duty: 0.769, Freq: 300751.88, Pin: 134.97
Algo: 0, Vpan: 13.20, Ipan: 10.17, Vbat: 0.00, Ibat: 0.00, Duty: 0.776, Freq: 300751.88, Pin: 134.28
Algo: 0, Vpan: 13.79, Ipan: 9.78, Vbat: 0.00, Ibat: 0.00, Duty: 0.769, Freq: 300751.88, Pin: 134.86
Setting gain of channel 0: 2.048000
busy
Algo: 0, Vpan: 13.02, Ipan: 9.26, Vbat: 0.00, Ibat: 0.00, Duty: 0.769, Freq: 300751.88, Pin: 120.49
Algo: 0, Vputy: 0.769, Freq: 300751.88, Pin: 83.76
an: 10.87, Ipan: 7.70, Vbat: 0.00, Ibat: 0.00, DAlgo: 0, Vpan: 10.80, Ipan: 7.63, Vbat: 0.00, Ibat: 0.00, Duty: 0.769, Freq: 300751.88, Pin: 82.42
Algo: 0, Vpan: 10.78, Ipan: 7.62, Vbat: 0.00, Ibat: 0.00, Duty: 0.769, Freq: 300751.88, Pin: 82.07
Algo: 0, Vpan: 10.76, Ipan: 7.60, Vbat: 0.00, Ibat: 0.00, Duty: 0.769, Freq: 300751.88, Pin: 81.82
Algo: 0, Vpan: 10.75, Ipan: 7.60, Vbat: 0.00, Ibat: 0.00, Duty: 0.769, Freq: 300751.88, Pin: 81.67
Algo: 0, Vpan: 10.74, Ipan: 7.59, Vbat: 0.00, Ibat: 0.00, Duty: 0.769, Freq: 300751.88, Pin: 81.50
Algo: 0, Vpan: 10.73, Ipan: 7.58, Vbat: 0.00, Ibat: 0.00, Duty: 0.769, Freq: 300751.88, Pin: 81.38
Algo: 0, Vpan: 10.73, Ipan: 7.58, Vbat: 0.00, Ibat: 0.00, Duty: 0.769, Freq: 300751.88, Pin: 81.26
Algo: 0, Vpan: 10.72, Ipan: 7.57, Vbat: 0.00, Ibat: 0.00, Duty: 0.769, Freq: 300751.88, Pin: 81.13
Algo: 0, Vpan: 10.71, Ipan: 7.57, Vbat: 0.00, Ibat: 0.00, Duty: 0.769, Freq: 300751.88, Pin: 81.03
Algo: 0, Vpan: 10.71, Ipan: 7.56, Vbat: 0.00, Ibat: 0.00, Duty: 0.769, Freq: 300751.88, Pin: 80.93
Algo: 0, Vpan: 10.70, Ipan: 7.56, Vbat: 0.00, Ibat: 0.00, Duty: 0.769, Freq: 300751.88, Pin: 80.89
Algo: 0, Vpan: 10.70, Ipan: 7.55, Vbat: 0.00, Ibat: 0.00, Duty: 0.769, Freq: 300751.88, Pin: 80.77
Algo: 0, Vpan: 10.68, Ipan: 7.55, Vbat: 0.00, Ibat: 0.00, Duty: 0.769, Freq: 300751.88, Pin: 80.63
Algo: 0, V

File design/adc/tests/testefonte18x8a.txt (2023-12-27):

Algo: 0, Vpan: 14.78, Ipan: 7.33, Vbat: 0.00, Ibat: 0.00, Duty: 0.731, Freq: 300751.88, Pin: 108.32
Setting gain of channel 2: 0.512000
busy
Algo: 0, Vpan: 15.41, Ipan: 7.06, Vbat: 0.00, Ibat: 0.00, Duty: 0.724, Freq: 300751.88, Pin: 108.81
Setting gain of channel 2: 0.256000
busy
Algo: 0, Vpan: 15.84, Ipan: 6.74, Vbat: 0.00, Ibat: 0.00, Duty: 0.716, Freq: 300751.88, Pin: 106.73
�b����� 15.46, Ipan: 7.08, Vbat: 0.00, Ibat: 0.00, Duty: 0.724, Freq: 300751.88, Pin: 109.47
INFO: ==> STATE INITIALIZING
INFO: ==> STATE IDLE
Setting gain of channel 0: 2.048000
INFO: ==> STATE RUNNING
Setting gain of channel 1: 2.048000
busy
Setting gain of channel 2: 2.048000
busy
Setting gain of channel 3: 2.048000
Algo: 2, Vpan: 20.04, Ipan: 0.05, Vbat: 0.00, Ibat: 0.00, Duty: 0.000, Freq: 300751.88, Pin: 1.07
Setting gain of channel 0: 1.024000
busy
Setting gain of channel 2: 1.024000
busy
Setting gain of channel 2: 0.512000
busy
Algo: 2, Vpan: 18.53, Ipan: 2.67, Vbat: 0.00, Ibat: 0.00, Duty: 0.627, Freq: 300751.88, Pin: 49.40
Setting gain of channel 2: 0.256000
busy
Algo: 2, Vpan: 18.16, Ipan: 4.46, Vbat: 0.00, Ibat: 0.00, Duty: 0.657, Freq: 300751.88, Pin: 80.98
Setting gain of channel 0: 2.048000
busy
Algo: 2, Vpan: 17.16, Ipan: 5.06, Vbat: 0.00, Ibat: 0.00, Duty: 0.687, Freq: 300751.88, Pin: 86.80
Algo: 2, Vpan: 15.92, Ipan: 6.77, Vbat: 0.00, Ibat: 0.00, Duty: 0.716, Freq: 300751.88, Pin: 107.86
Algo: 2, Vpan: 13.89, Ipan: 8.19, Vbat: 0.00, Ibat: 0.00, Duty: 0.746, Freq: 300751.88, Pin: 113.75
Setting gain of channel 1: 1.024000
busy
Algo: 2, Vpan: 10.02, Ipan: 7.89, Vbat: 0.00, Ibat: 0.00, Duty: 0.776, Freq: 300751.88, Pin: 79.03
Setting gain of channel 2: 0.512000
busy
Algo: 2, Vpan: 7.90, Ipan: 8.03, Vbat: 0.00, Ibat: 0.00, Duty: 0.799, Freq: 300751.88, Pin: 63.41
Setting gain of channel 1: 2.048000
busy
Algo: 2, Vpan: 9.92, Ipan: 7.76, Vbat: 0.00, Ibat: 0.00, Duty: 0.769, Freq: 300751.88, Pin: 77.02
Setting gain of channel 2: 0.256000
busy
Brute force done!
Algo: 2, Vpan: 13.74, Ipan: 7.44, Vbat: 0.00, Ibat: 0.00, Duty: 0.739, Freq: 300751.88, Pin: 102.16
Algo: 0, Vpan: 13.78, Ipan: 7.33, Vbat: 0.00, Ibat: 0.00, Duty: 0.739, Freq: 300751.88, Pin: 101.06
Algo: 0, Vpan: 12.89, Ipan: 7.46, Vbat: 0.00, Ibat: 0.00, Duty: 0.746, Freq: 300751.88, Pin: 96.19
Algo: 0, Vpan: 12.87, Ipan: 7.46, Vbat: 0.00, Ibat: 0.00, Duty: 0.746, Freq: 300751.88, Pin: 96.02
Algo: 0, Vpan: 12.86, Ipan: 7.45, Vbat: 0.00, Ibat: 0.00, Duty: 0.746, Freq: 300751.88, Pin: 95.83
Algo: 0, Vpan: 12.86, Ipan: 7.45, Vbat: 0.00, Ibat: 0.00, Duty: 0.746, Freq: 300751.88, Pin: 95.71
Algo: 0, Vpan: 12.85, Ipan: 7.44, Vbat: 0.00, Ibat: 0.00, Duty: 0.746, Freq: 300751.88, Pin: 95.65
Algo: 0, Vpan: 12.85, Ipan: 7.44, Vbat: 0.00, Ibat: 0.00, Duty: 0.746, Freq: 300751.88, Pin: 95.55
Algo: 0, Vpan: 12.84, Ipan: 7.44, Vbat: 0.00, Ibat: 0.00, Duty: 0.746, Freq: 300751.88, Pin: 95.48
Algo: 0, Vpan: 12.83, Ipan: 7.43, Vbat: 0.00, Ibat: 0.00, Duty: 0.746, Freq: 300751.88, Pin: 95.33
Algo: 0, Vpan: 12.82, Ipan: 7.43, Vbat: 0.00, Ibat: 0.00, Duty: 0.746, Freq: 300751.88, Pin: 95.24
Algo: 0, Vpan: 12.82, Ipan: 7.42, Vbat: 0.00, Ibat: 0.00, Duty: 0.746, Freq: 300751.88, Pin: 95.18
Setting gain of channel 2: 0.512000
busy
Algo: 0, Vpan: 12.83, Ipan: 7.42, Vbat: 0.00, Ibat: 0.00, Duty: 0.746, Freq: 300751.88, Pin: 95.16
Setting gain of channel 2: 0.256000
busy
Algo: 0, Vpan: 12.81, Ipan: 7.42, Vbat: 0.00, Ibat: 0.00, Duty: 0.746, Freq: 300751.88, Pin: 95.03
Setting gain of channel 2: 0.512000
busy
Algo: 0, Vpan: 12.82, Ipan: 7.41, Vbat: 0.00, Ibat: 0.00, Duty: 0.746, Freq: 300751.88, Pin: 95.05
Algo: 0, Vpan: 12.15, Ipan: 7.49, Vbat: 0.00, Ibat: 0.00, Duty: 0.754, Freq: 300751.88, Pin: 91.01
Setting gain of channel 2: 0.256000
busy
Setting gain of channel 2: 0.512000
busy
Algo: 0, Vpan: 12.74, Ipan: 7.41, Vbat: 0.00, Ibat: 0.00, Duty: 0.746, Freq: 300751.88, Pin: 94.40
Setting gain of channel 2: 1.024000
busy
Setting gain of channel 2: 0.512000
busy
Algo: 0, Vpan: 12.80, Ipan: 7.41, Vbat: 0.00, Ibat: 0.00, Duty: 0.746, Freq: 300751.88, Pin: 94.82
Algo: 0, Vpan: 13.70, Ipan: 7.28, Vbat: 0.00, Ibat: 0.00, Duty: 0.739, Freq: 300751.88, Pin: 99.71
Setting gain of channel 2: 1.024000
busy
Algo: 0, Vpan: 14.50, Ipan: 7.17, Vbat: 0.00, Ibat: 0.00, Duty: 0.731, Freq: 300751.88, Pin: 103.97
Setting gain of channel 2: 0.512000
busy
Setting gain of channel 2: 1.024000
busy
Algo: 0, Vpan: 15.34, Ipan: 7.04, Vbat: 0.00, Ibat: 0.00, Duty: 0.724, Freq: 300751.88, Pin: 107.96
Setting gain of channel 2: 0.512000
busy
Setting gain of channel 2: 0.256000
busy
Setting gain of channel 2: 0.512000
busy
Algo: 0, Vpan: 15.35, Ipan: 7.03, Vbat: 0.00, Ibat: 0.00, Duty: 0.724, Freq: 300751.88, Pin: 107.88
Setting gain of channel 2: 0.256000
busy
Setting gain of channel 2: 0.512000
busy
Algo: 0, Vpan: 15.36, Ipan: 7.03, Vbat: 0.00, Ibat: 0.00, Duty: 0.724, Freq: 300751.88, Pin: 108.01
Setting gain of channel 2: 0.256000
busy
Setting gain of channel 2: 0.512000
busy
Algo: 0, Vpan: 14.54, Ipan: 7.16, Vbat: 0.00, Ibat: 0.00, Duty: 0.731, Freq: 300751.88, Pin: 104.14
Algo: 0, Vpan: 15.37, Ipan: 7.03, Vbat: 0.00, Ibat: 0.00, Duty: 0.724, Freq: 300751.88, Pin: 108.09
Algo: 0, Vpan: 15.37, Ipan: 7.03, Vbat: 0.00, Ibat: 0.00, Duty: 0.724, Freq: 300751.88, Pin: 108.13
Algo: 0, Vpan: 15.85, Ipan: 6.74, Vbat: 0.00, Ibat: 0.00, Duty: 0.716, Freq: 300751.88, Pin: 106.85
Algo: 0, Vpan: 15.51, Ipan: 7.09, Vbat: 0.00, Ibat: 0.00, Duty: 0.724, Freq: 300751.88, Pin: 110.05
Algo: 0, Vpan: 15.51, Ipan: 7.09, Vbat: 0.00, Ibat: 0.00, Duty: 0.724, Freq: 300751.88, Pin: 109.99
Algo: 0, Vpan: 15.39, Ipan: 7.04, Vbat: 0.00, Ibat: 0.00, Duty: 0.724, Freq: 300751.88, Pin: 108.32
Algo: 0, Vpan: 15.39, Ipan: 7.04, Vbat: 0.00, Ibat: 0.00, Duty: 0.724, Freq: 300751.88, Pin: 108.30
Algo: 0, Vpan: 15.40, Ipan: 7.04, Vbat: 0.00, Ibat: 0.00, Duty: 0.724, Freq: 300751.88, Pin: 108.35
Algo: 0, Vpan: 15.91, Ipan: 6.74, Vbat: 0.00, Ibat: 0.00, Duty: 0.716, Freq: 300751.88, Pin: 107.21
Algo: 0, Vpan: 15.52, Ipan: 7.06, Vbat: 0.00, Ibat: 0.00, Duty: 0.724, Freq: 300751.88, Pin: 109.55
Algo: 0, Vpan: 15.52, Ipan: 7.09, Vbat: 0.00, Ibat: 0.00, Duty: 0.724, Freq: 300751.88, Pin: 110.01
Algo: 0, Vpan: 14.58, Ipan: 7.18, Vbat: 0.00, Ibat: 0.00, Duty: 0.731, Freq: 300751.88, Pin: 104.72
Algo: 0, Vpan: 15.40, Ipan: 7.04, Vbat: 0.00, Ibat: 0.00, Duty: 0.724, Freq: 300751.88, Pin: 108.37
Algo: 0, Vpan: 15.41, Ipan: 7.04, Vbat: 0.00, Ibat: 0.00, Duty: 0.724, Freq: 300751.88, Pin: 108.43
Algo: 0, Vpan: 15.86, Ipan: 6.73, Vbat: 0.00, Ibat: 0.00, Duty: 0.716, Freq: 300751.88, Pin: 106.80
Algo: 0, Vpan: 15.52, Ipan: 7.09, Vbat: 0.00, Ibat: 0.00, Duty: 0.724, Freq: 300751.88, Pin: 110.03
Algo: 0, Vpan: 15.52, Ipan: 7.09, Vbat: 0.00, Ibat: 0.00, Duty: 0.724, Freq: 300751.88, Pin: 110.01
Algo: 0, Vpan: 15.45, Ipan: 7.05, Vbat: 0.00, Ibat: 0.00, Duty: 0.724, Freq: 300751.88, Pin: 108.91
Algo: 0, Vpan: 15.42, Ipan: 7.04, Vbat: 0.00, Ibat: 0.00, Duty: 0.724, Freq: 300751.88, Pin: 108.50
Algo: 0, Vpan: 15.42, Ipan: 7.04, Vbat: 0.00, Ibat: 0.00, Duty: 0.724, Freq: 300751.88, Pin: 108.53
Algo: 0, Vpan: 15.91, Ipan: 6.73, Vbat: 0.00, Ibat: 0.00, Duty: 0.716, Freq: 300751.88, Pin: 107.07
Algo: 0, Vpan: 15.53, Ipan: 7.05, Vbat: 0.00, Ibat: 0.00, Duty: 0.724, Freq: 300751.88, Pin: 109.45
Algo: 0, Vpan: 15.53, Ipan: 7.08, Vbat: 0.00, Ibat: 0.00, Duty: 0.724, Freq: 300751.88, Pin: 109.93
Setting gain of channel 2: 1.024000
busy
Setting gain of channel 2: 0.512000
busy
Algo: 0, Vpan: 14.64, Ipan: 7.20, Vbat: 0.00, Ibat: 0.00, Duty: 0.731, Freq: 300751.88, Pin: 105.45
Setting gain of channel 2: 1.024000
busy
Setting gain of channel 2: 0.512000
busy
Algo: 0, Vpan: 15.34, Ipan: 7.03, Vbat: 0.00, Ibat: 0.00, Duty: 0.724, Freq: 300751.88, Pin: 107.92
Setting gain of channel 2: 1.024000
busy
Setting gain of channel 2: 0.512000
busy
Algo: 0, Vpan: 15.43, Ipan: 7.03, Vbat: 0.00, Ibat: 0.00, Duty: 0.724, Freq: 300751.88, Pin: 108.53
Setting gain of channel 2: 1.024000
busy
Setting gain of channel 2: 0.512000
busy
Algo: 0, Vpan: 15.91, Ipan: 6.72, Vbat: 0.00, Ibat: 0.00, Duty: 0.716, Freq: 300751.88, Pin: 106.92
Setting gain of channel 2: 1.024000
busy
Algo: 0, Vpan: 15.52, Ipan: 7.07, Vbat: 0.00, Ibat: 0.00, Duty: 0.724, Freq: 300751.88, Pin: 109.78
Setting gain of channel 2: 0.512000
busy
Setting gain of channel 2: 1.024000
busy
Setting gain of channel 2: 0.512000
busy
Setting gain of channel 2: 1.024000
busy
Algo: 0, Vpan: 15.52, Ipan: 7.07, Vbat: 0.00, Ibat: 0.00, Duty: 0.724, Freq: 300751.88, Pin: 109.77
Setting gain of channel 2: 0.512000
busy
Setting gain of channel 2: 1.024000
busy
Setting gain of channel 2: 0.512000
busy
Setting gain of channel 2: 1.024000
busy
Algo: 0, Vpan: 15.52, Ipan: 7.07, Vbat: 0.00, Ibat: 0.00, Duty: 0.724, Freq: 300751.88, Pin: 109.76
Setting gain of channel 2: 0.512000
busy
Setting gain of channel 2: 1.024000
busy
Setting gain of channel 2: 0.512000
Algo: 0, Vpan: 15.44, Ipan: 7.04, Vbat: 0.00, Ibat: 0.00, Duty: 0.724, Freq: 300751.88, Pin: 108.66
Setting gain of channel 2: 1.024000
busy
Setting gain of channel 2: 0.512000
busy
Setting gain of channel 2: 1.024000
busy
Algo: 0, Vpan: 15.43, Ipan: 7.03, Vbat: 0.00, Ibat: 0.00, Duty: 0.724, Freq: 300751.88, Pin: 108.53
Setting gain of channel 2: 0.512000
busy
Setting gain of channel 2: 1.024000
busy
Algo: 0, Vpan: 15.43, Ipan: 7.03, Vbat: 0.00, Ibat: 0.00, Duty: 0.724, Freq: 300751.88, Pin: 108.51
Setting gain of channel 2: 0.512000
busy
Setting gain of channel 2: 1.024000
busy
Setting gain of channel 2: 0.512000
Algo: 0, Vpan: 15.44, Ipan: 7.03, Vbat: 0.00, Ibat: 0.00, Duty: 0.724, Freq: 300751.88, Pin: 108.51
Setting gain of channel 2: 1.024000
busy
Setting gain of channel 2: 0.512000
busy
Setting gain of channel 2: 1.024000
busy
Algo: 0, Vpan: 15.91, Ipan: 6.72, Vbat: 0.00, Ibat: 0.00, Duty: 0.716, Freq: 300751.88, Pin: 106.85
Setting gain of channel 2: 0.512000
busy
Setting gain of channel 2: 1.024000
busy
Setting gain of channel 2: 0.512000
busy
Setting gain of channel 2: 1.024000
busy
Algo: 0, Vpan: 15.57, Ipan: 7.07, Vbat: 0.00, Ibat: 0.00, Duty: 0.724, Freq: 300751.88, Pin: 110.07
Setting gain of channel 2: 0.512000
busy
Setting gain of channel 2: 1.024000
busy
Algo: 0, Vpan: 15.53, Ipan: 7.07, Vbat: 0.00, Ibat: 0.00, Duty: 0.724, Freq: 300751.88, Pin: 109.78
Algo: 0, Vpan: 15.53, Ipan: 7.07, Vbat: 0.00, Ibat: 0.00, Duty: 0.724, Freq: 300751.88, Pin: 109.76
Setting gain of channel 2: 0.512000
busy
Setting gain of channel 2: 1.024000
busy
Algo: 0, Vpan: 15.51, Ipan: 7.06, Vbat: 0.00, Ibat: 0.00, Duty: 0.724, Freq: 300751.88, Pin: 109.48
Setting gain of channel 2: 0.512000
busy
Setting gain of channel 2: 1.024000
busy
Algo: 0, Vpan: 15.46, Ipan: 7.04, Vbat: 0.00, Ibat: 0.00, Duty: 0.724, Freq: 300751.88, Pin: 108.77
Setting gain of channel 2: 0.512000
busy
Setting gain of channel 2: 1.024000
busy
Setting gain of channel 2: 0.512000
busy
Algo: 0, Vpan: 15.46, Ipan: 7.03, Vbat: 0.00, Ibat: 0.00, Duty: 0.724, Freq: 300751.88, Pin: 108.73
Setting gain of channel 2: 1.024000
busy
Setting gain of channel 2: 0.512000
busy
Setting gain of channel 2: 1.024000
busy
Algo: 0, Vpan: 15.46, Ipan: 7.03, Vbat: 0.00, Ibat: 0.00, Duty: 0.724, Freq: 300751.88, Pin: 108.68
Setting gain of channel 2: 0.512000
busy
Setting gain of channel 2: 1.024000
busy
Algo: 0, Vpan: 15.46, Ipan: 7.03, Vbat: 0.00, Ibat: 0.00, Duty: 0.724, Freq: 300751.88, Pin: 108.69
Setting gain of channel 2: 0.512000
busy
Setting gain of channel 2: 1.024000
busy
Setting gain of channel 2: 0.512000
busy
Setting gain of channel 2: 1.024000
busy
Algo: 0, Vpan: 14.63, Ipan: 7.18, Vbat: 0.00, Ibat: 0.00, Duty: 0.731, Freq: 300751.88, Pin: 105.02
Setting gain of channel 2: 0.512000
busy
Setting gain of channel 2: 1.024000
busy
Setting gain of channel 2: 0.512000
Algo: 0, Vpan: 15.46, Ipan: 7.05, Vbat: 0.00, Ibat: 0.00, Duty: 0.724, Freq: 300751.88, Pin: 108.89
Setting gain of channel 2: 1.024000
busy
Algo: 0, Vpan: 15.46, Ipan: 7.03, Vbat: 0.00, Ibat: 0.00, Duty: 0.724, Freq: 300751.88, Pin: 108.71
Setting gain of channel 2: 0.512000
busy
Setting gain of channel 2: 1.024000
busy
Setting gain of channel 2: 0.512000
busy
Setting gain of channel 2: 1.024000
busy
Algo: 0, Vpan: 15.46, Ipan: 7.03, Vbat: 0.00, Ibat: 0.00, Duty: 0.724, Freq: 300751.88, Pin: 108.72
Setting gain of channel 2: 0.512000
busy
Setting gain of channel 2: 1.024000
busy
Setting gain of channel 2: 0.512000
Algo: 0, Vpan: 14.64, Ipan: 7.16, Vbat: 0.00, Ibat: 0.00, Duty: 0.731, Freq: 300751.88, Pin: 104.80
Setting gain of channel 2: 1.024000
busy
Setting gain of channel 2: 0.512000
busy
Setting gain of channel 2: 1.024000
busy
Algo: 0, Vpan: 15.46, Ipan: 7.03, Vbat: 0.00, Ibat: 0.00, Duty: 0.724, Freq: 300751.88, Pin: 108.63
Setting gain of channel 2: 0.512000
busy
Setting gain of channel 2: 1.024000
busy
Algo: 0, Vpan: 15.46, Ipan: 7.03, Vbat: 0.00, Ibat: 0.00, Duty: 0.724, Freq: 300751.88, Pin: 108.64
Setting gain of channel 2: 0.512000
busy
Setting gain of channel 2: 1.024000
busy
Algo: 0, Vpan: 15.92, Ipan: 6.74, Vbat: 0.00, Ibat: 0.00, Duty: 0.716, Freq: 300751.88, Pin: 107.26
Setting gain of channel 2: 0.512000
busy
Setting gain of channel 2: 1.024000
busy
Algo: 0, Vpan: 15.53, Ipan: 7.06, Vbat: 0.00, Ibat: 0.00, Duty: 0.724, Freq: 300751.88, Pin: 109.64
Setting gain of channel 2: 0.512000
busy
Setting gain of channel 2: 1.024000
busy
Algo: 0, Vpan: 15.53, Ipan: 7.06, Vbat: 0.00, Ibat: 0.00, Duty: 0.724, Freq: 300751.88, Pin: 109.62
Setting gain of channel 2: 0.512000
busy
Setting gain of channel 2: 1.024000
busy
Algo: 0, Vpan: 15.53, Ipan: 7.06, Vbat: 0.00, Ibat: 0.00, Duty: 0.724, Freq: 300751.88, Pin: 109.60
Setting gain of channel 2: 0.512000
busy
Setting gain of channel 2: 1.024000
busy
Algo: 0, Vpan: 15.53, Ipan: 7.05, Vbat: 0.00, Ibat: 0.00, Duty: 0.724, Freq: 300751.88, Pin: 109.57
Setting gain of channel 2: 0.512000
busy
Setting gain of channel 2: 1.024000
busy
Algo: 0, Vpan: 15.47, Ipan: 7.03, Vbat: 0.00, Ibat: 0.00, Duty: 0.724, Freq: 300751.88, Pin: 108.73
Setting gain of channel 2: 0.512000
busy
Setting gain of channel 2: 1.024000
busy
Algo: 0, Vpan: 15.47, Ipan: 7.03, Vbat: 0.00, Ibat: 0.00, Duty: 0.724, Freq: 300751.88, Pin: 108.75
Algo: 0, Vpan: 14.72, Ipan: 7.17, Vbat: 0.00, Ibat: 0.00, Duty: 0.731, Freq: 300751.88, Pin: 105.59
Setting gain of channel 2: 0.512000
busy
Setting gain of channel 2: 1.024000
busy
Setting gain of channel 2: 0.512000
busy
Setting gain of channel 2: 1.024000
busy
Algo: 0, Vpan: 15.47, Ipan: 7.03, Vbat: 0.00, Ibat: 0.00, Duty: 0.724, Freq: 300751.88, Pin: 108.70
Setting gain of channel 2: 0.512000
busy
Setting gain of channel 2: 1.024000
busy
Algo: 0, Vpan: 15.48, Ipan: 7.02, Vbat: 0.00, Ibat: 0.00, Duty: 0.724, Freq: 300751.88, Pin: 108.71
Setting gain of channel 2: 0.512000
busy
Setting gain of channel 2: 1.024000
busy
Setting gain of channel 2: 0.512000
busy
Setting gain of channel 2: 1.024000
busy
Algo: 0, Vpan: 15.92, Ipan: 6.70, Vbat: 0.00, Ibat: 0.00, Duty: 0.716, Freq: 300751.88, Pin: 106.65
Setting gain of channel 2: 0.512000
busy
Setting gain of channel 2: 1.024000
busy
Setting gain of channel 2: 0.512000
busy
Algo: 0, Vpan: 15.53, Ipan: 7.05, Vbat: 0.00, Ibat: 0.00, Duty: 0.724, Freq: 300751.88, Pin: 109.52
Setting gain of channel 2: 1.024000
busy
Setting gain of channel 2: 0.512000
busy
Setting gain of channel 2: 1.024000
busy
Algo: 0, Vpan: 15.53, Ipan: 7.05, Vbat: 0.00, Ibat: 0.00, Duty: 0.724, Freq: 300751.88, Pin: 109.53
Setting gain of channel 2: 0.512000
busy
Setting gain of channel 2: 1.024000
busy
Algo: 0, Vpan: 14.81, Ipan: 7.26, Vbat: 0.00, Ibat: 0.00, Duty: 0.731, Freq: 300751.88, Pin: 107.61
Algo: 0, Vpan: 15.48, Ipan: 7.02, Vbat: 0.00, Ibat: 0.00, Duty: 0.724, Freq: 300751.88, Pin: 108.70
Algo: 0, Vpan: 15.48, Ipan: 7.02, Vbat: 0.00, Ibat: 0.00, Duty: 0.724, Freq: 300751.88, Pin: 108.77
Setting gain of channel 2: 0.512000
busy
Setting gain of channel 2: 1.024000
busy
Setting gain of channel 2: 0.512000
busy
Algo: 0, Vpan: 15.92, Ipan: 6.73, Vbat: 0.00, Ibat: 0.00, Duty: 0.716, Freq: 300751.88, Pin: 107.13
Setting gain of channel 2: 1.024000
busy
Algo: 0, Vpan: 15.54, Ipan: 7.05, Vbat: 0.00, Ibat: 0.00, Duty: 0.724, Freq: 300751.88, Pin: 109.49
Algo: 0, Vpan: 15.54, Ipan: 7.04, Vbat: 0.00, Ibat: 0.00, Duty: 0.724, Freq: 300751.88, Pin: 109.45
Algo: 0, Vpan: 15.54, Ipan: 7.05, Vbat: 0.00, Ibat: 0.00, Duty: 0.724, Freq: 300751.88, Pin: 109.47
Setting gain of channel 2: 0.512000
busy
Setting gain of channel 2: 1.024000
busy
Setting gain of channel 2: 0.512000
busy
Setting gain of channel 2: 1.024000
busy
Algo: 0, Vpan: 15.93, Ipan: 6.73, Vbat: 0.00, Ibat: 0.00, Duty: 0.716, Freq: 300751.88, Pin: 107.14
Setting gain of channel 2: 0.512000
busy
Setting gain of channel 2: 1.024000
busy
Setting gain of channel 2: 0.512000
busy
Setting gain of channel 2: 1.024000
busy
Algo: 0, Vpan: 15.57, Ipan: 7.04, Vbat: 0.00, Ibat: 0.00, Duty: 0.724, Freq: 300751.88, Pin: 109.68
Setting gain of channel 2: 0.512000
busy
Setting gain of channel 2: 1.024000
busy
Setting gain of channel 2: 0.512000
busy
Setting gain of channel 2: 1.024000
busy
Algo: 0, Vpan: 15.54, Ipan: 7.04, Vbat: 0.00, Ibat: 0.00, Duty: 0.724, Freq: 300751.88, Pin: 109.39
Setting gain of channel 2: 0.512000
busy
Setting gain of channel 2: 1.024000
busy
Setting gain of channel 2: 0.512000
busy
Setting gain of channel 2: 1.024000
busy
Algo: 0, Vpan: 15.53, Ipan: 7.04, Vbat: 0.00, Ibat: 0.00, Duty: 0.724, Freq: 300751.88, Pin: 109.37
Setting gain of channel 2: 0.512000
busy
Setting gain of channel 2: 1.024000
busy
Setting gain of channel 2: 0.512000
busy
Algo: 0, Vpan: 15.53, Ipan: 7.04, Vbat: 0.00, Ibat: 0.00, Duty: 0.724, Freq: 300751.88, Pin: 109.32
Setting gain of channel 2: 1.024000
busy
Setting gain of channel 2: 0.512000
busy
Setting gain of channel 2: 1.024000
busy
Algo: 0, Vpan: 15.53, Ipan: 7.04, Vbat: 0.00, Ibat: 0.00, Duty: 0.724, Freq: 300751.88, Pin: 109.31
Setting gain of channel 2: 0.512000
busy
Setting gain of channel 2: 0.256000
busy
Algo: 0, Vpan: 15.53, Ipan: 7.04, Vbat: 0.00, Ibat: 0.00, Duty: 0.724, Freq: 300751.88, Pin: 109.28
Algo: 0, Vpan: 15.53, Ipan: 7.04, Vbat: 0.00, Ibat: 0.00, Duty: 0.724, Freq: 300751.88, Pin: 109.30
Algo: 0, Vpan: 15.92, Ipan: 6.72, Vbat: 0.00, Ibat: 0.00, Duty: 0.716, Freq: 300751.88, Pin: 106.94
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

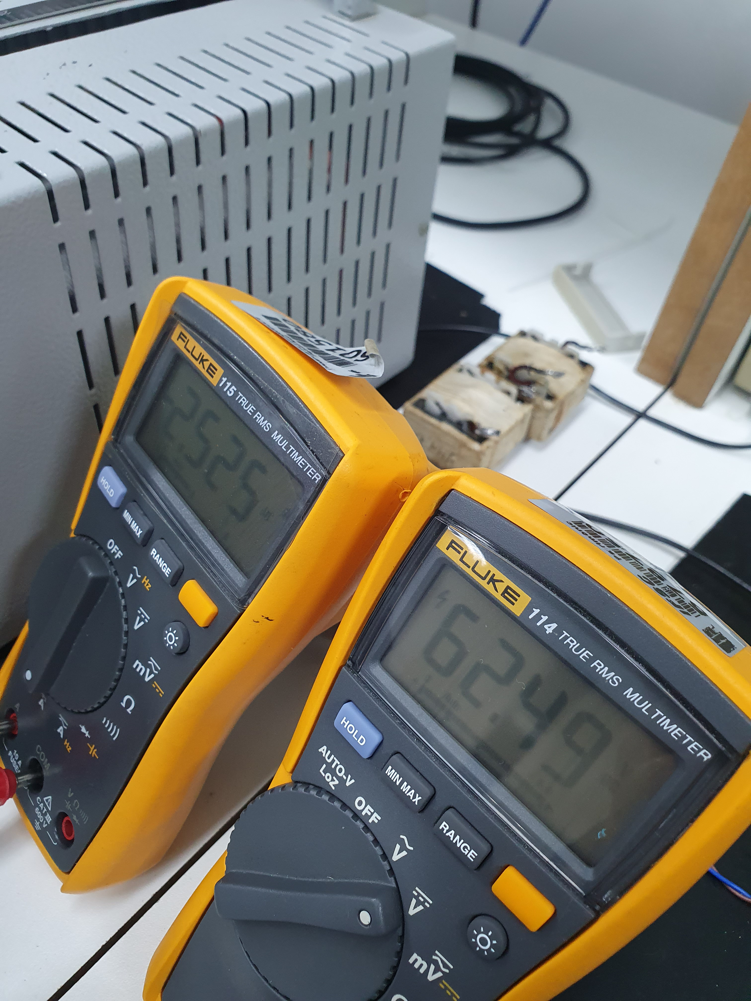
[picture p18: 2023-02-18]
tests/Test_without_snubber/200khz/output.jpg

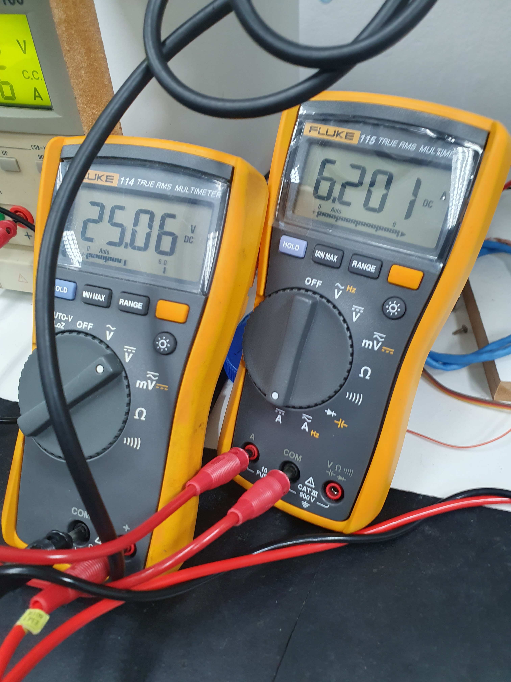
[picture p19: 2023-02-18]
tests/Test_without_snubber/400khz/input.jpg

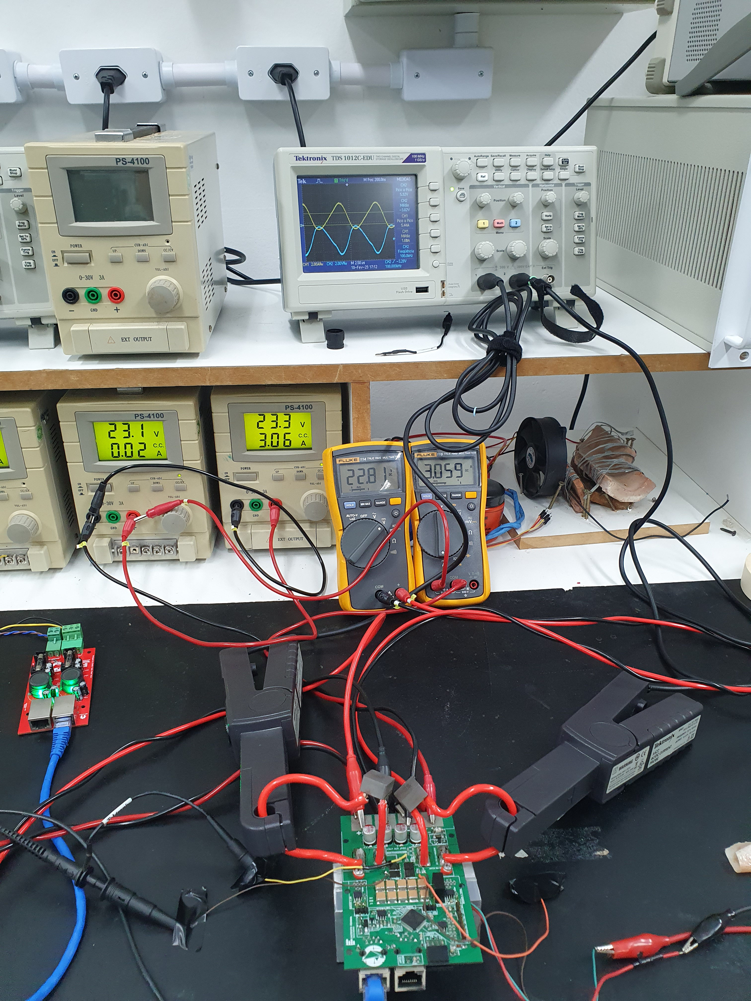
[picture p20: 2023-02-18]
tests/Test_with_snubber/100khz(22uH)/input.jpg

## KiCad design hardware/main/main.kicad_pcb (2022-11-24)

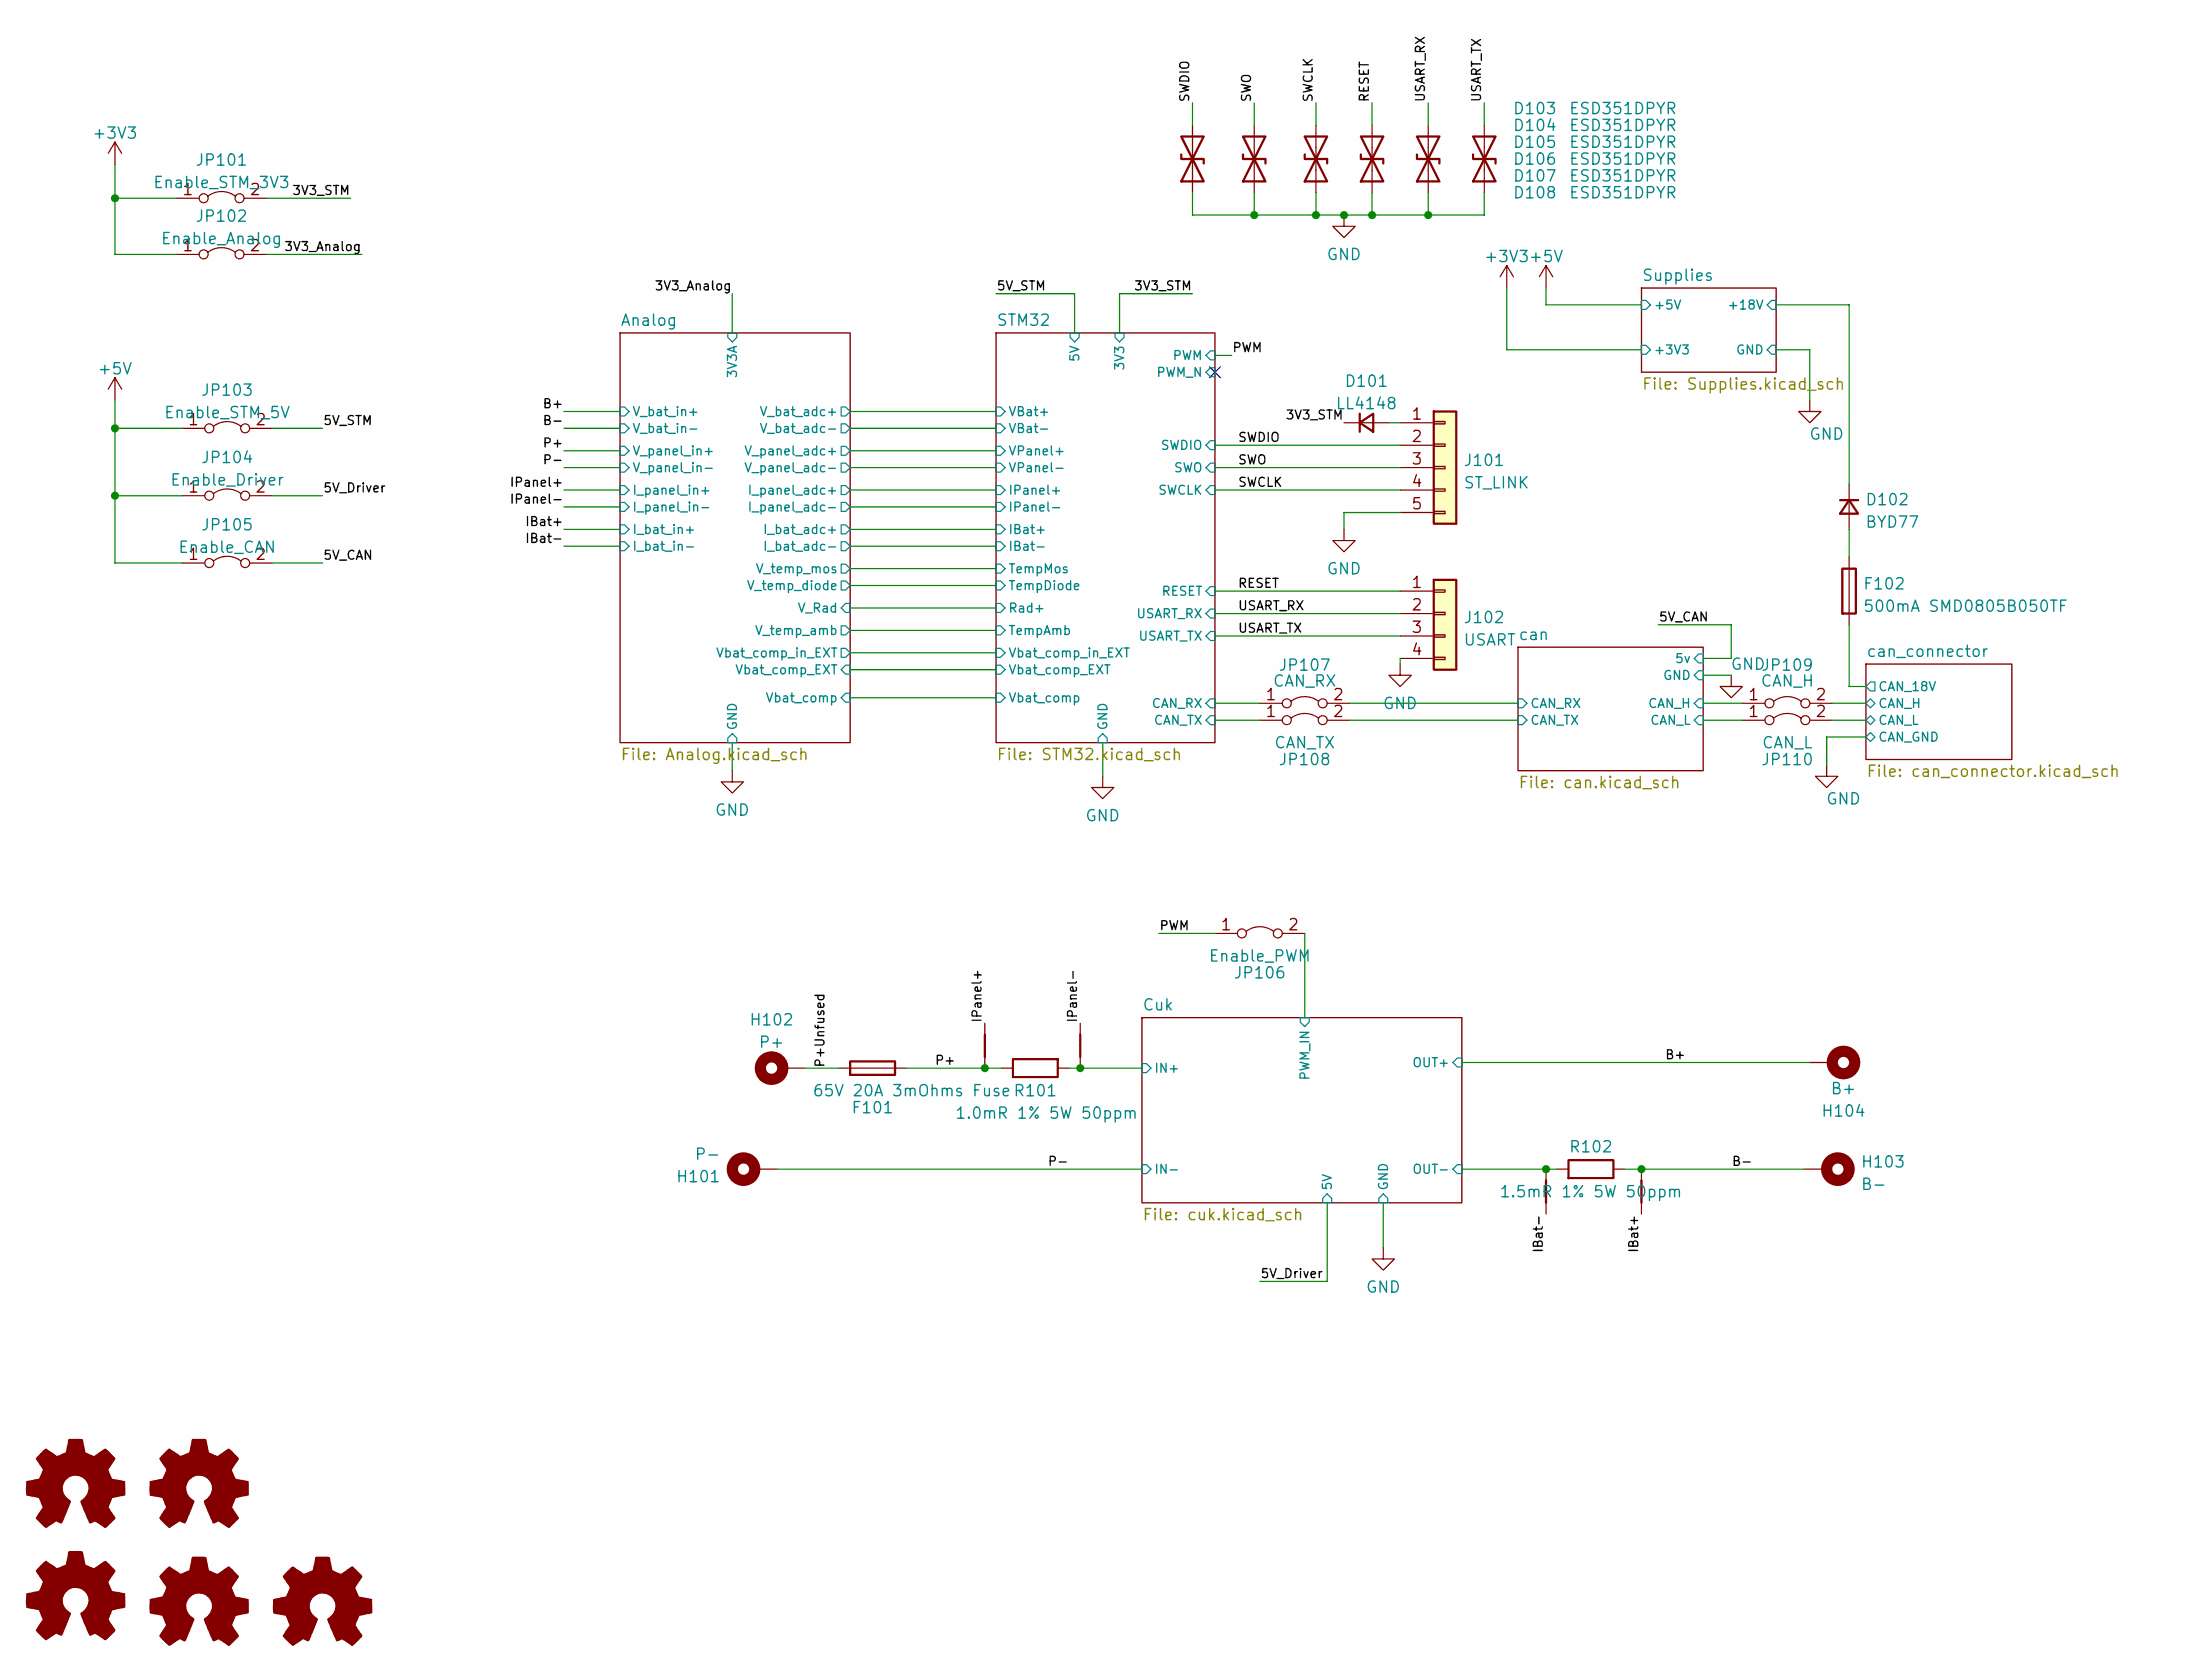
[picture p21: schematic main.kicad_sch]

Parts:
D101: LL4148; D_MiniMELF_Handsoldering
D102: BYD77; D_MiniMELF_Handsoldering
D103, D104, D105, D106, D107, D108: ESD351DPYR; D_0402_1005Metric_Pad0.77x0.64mm_HandSolder
F101: 65V 20A 3mOhms Fuse; S6125-F
F102: 500mA SMD0805B050TF; Fuse_0805_2012Metric_Pad1.15x1.40mm_HandSolder
H101: P-; MountingHole_13mmx13mm_Rectangular
H102: P+; MountingHole_13mmx13mm_Rectangular
H103: B-; MountingHole_13mmx13mm_Rectangular
H104: B+; MountingHole_13mmx13mm_Rectangular
J101: ST_LINK; PinSocket_1x05_P2.54mm_Horizontal_SMD
J102: USART; PinSocket_1x04_P2.54mm_Horizontal_SMD
JP101: Enable_STM_3V3; SolderJumper-2_P0.5mm_Open_TrianglePad0.8x0.5mm
JP102: Enable_Analog; SolderJumper-2_P0.5mm_Open_TrianglePad0.8x0.5mm
JP103: Enable_STM_5V; SolderJumper-2_P0.5mm_Open_TrianglePad0.8x0.5mm
JP104: Enable_Driver; SolderJumper-2_P0.5mm_Open_TrianglePad0.8x0.5mm
JP105: Enable_CAN; SolderJumper-2_P0.5mm_Open_TrianglePad0.8x0.5mm
JP106: Enable_PWM; SolderJumper-2_P0.5mm_Open_TrianglePad0.8x0.5mm
JP107: CAN_RX; SolderJumper-2_P0.5mm_Open_TrianglePad0.8x0.5mm
JP108: CAN_TX; SolderJumper-2_P0.5mm_Open_TrianglePad0.8x0.5mm
JP109: CAN_H; SolderJumper-2_P0.5mm_Open_TrianglePad0.8x0.5mm
JP110: CAN_L; SolderJumper-2_P0.5mm_Open_TrianglePad0.8x0.5mm
LOGO101: Logo_Open_Hardware_Small; symbol_logoZenite
LOGO102: Logo_Open_Hardware_Small; synbol_logoifsc
LOGO103: Logo_Open_Hardware_Small; OSHW-Logo_5.7x6mm_SilkScreen
LOGO104: Logo_Open_Hardware_Small; symbol_logoZenite_small
LOGO105: Logo_Open_Hardware_Small; synbol_logoifsc_small
NT101, NT102, NT104: NetTie_2; NetTie-2_SMD_Pad0.3mm
NT103: Resistor_SMD:R_0201_0603Metric; NetTie-2_SMD_Pad0.3mm
R101: 1.0mR 1% 5W 50ppm; R_2512_6332Metric_Pad1.40x3.35mm_HandSolder
R102: 1.5mR 1% 5W 50ppm; R_2512_6332Metric_Pad1.40x3.35mm_HandSolder

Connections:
+3V3: JP101.1 (A), JP102.1 (A); also elsewhere on the board
+5V: JP103.1 (A), JP104.1 (A), JP105.1 (A); also elsewhere on the board
/3V3_Analog: JP102.2 (B); also elsewhere on the board
/3V3_STM: D101.1 (K), JP101.2 (B); also elsewhere on the board
/5V_CAN: JP105.2 (B); also elsewhere on the board
/5V_Driver: JP104.2 (B); also elsewhere on the board
/5V_STM: JP103.2 (B); also elsewhere on the board
/B+: H104.1; also elsewhere on the board
/B-: H103.1, NT104.2, R102.1; also elsewhere on the board
/Cuk/A: NT102.2, NT103.2, R101.2, R102.2; also elsewhere on the board
/Cuk/PWM_IN: JP106.2 (B); also elsewhere on the board
/IBat+: NT104.1; also elsewhere on the board
/IBat-: NT103.1; also elsewhere on the board
/IPanel+: NT101.1; also elsewhere on the board
/IPanel-: NT102.1; also elsewhere on the board
/P+: F101.1, NT101.2, R101.1; also elsewhere on the board
/P+Unfused: F101.2, H102.1
/P-: H101.1; also elsewhere on the board
/PWM: JP106.1 (A); also elsewhere on the board
/RESET: D106.2 (A2), J102.1; also elsewhere on the board
/STM32/CAN_RX: JP107.1 (A); also elsewhere on the board
/STM32/CAN_TX: JP108.1 (A); also elsewhere on the board
/SWCLK: D105.2 (A2), J101.4; also elsewhere on the board
/SWDIO: D103.2 (A2), J101.2; also elsewhere on the board
/SWO: D104.2 (A2), J101.3; also elsewhere on the board
/Supplies/+18V: D102.1 (K); also elsewhere on the board
/USART_RX: D107.2 (A2), J102.2; also elsewhere on the board
/USART_TX: D108.2 (A2), J102.3; also elsewhere on the board
/can/CAN_H: JP109.1 (A); also elsewhere on the board
/can/CAN_L: JP110.1 (A); also elsewhere on the board
/can/CAN_RX: JP107.2 (B); also elsewhere on the board
/can/CAN_TX: JP108.2 (B); also elsewhere on the board
/can_connector/CAN_18V: F102.2; also elsewhere on the board
/can_connector/CAN_H: JP109.2 (B); also elsewhere on the board
/can_connector/CAN_L: JP110.2 (B); also elsewhere on the board
GND: D103.1 (A1), D104.1 (A1), D105.1 (A1), D106.1 (A1), D107.1 (A1), D108.1 (A1), J101.5, J102.4; also elsewhere on the board
unnamed: D101.2 (A), J101.1
unnamed: D102.2 (A), F102.1

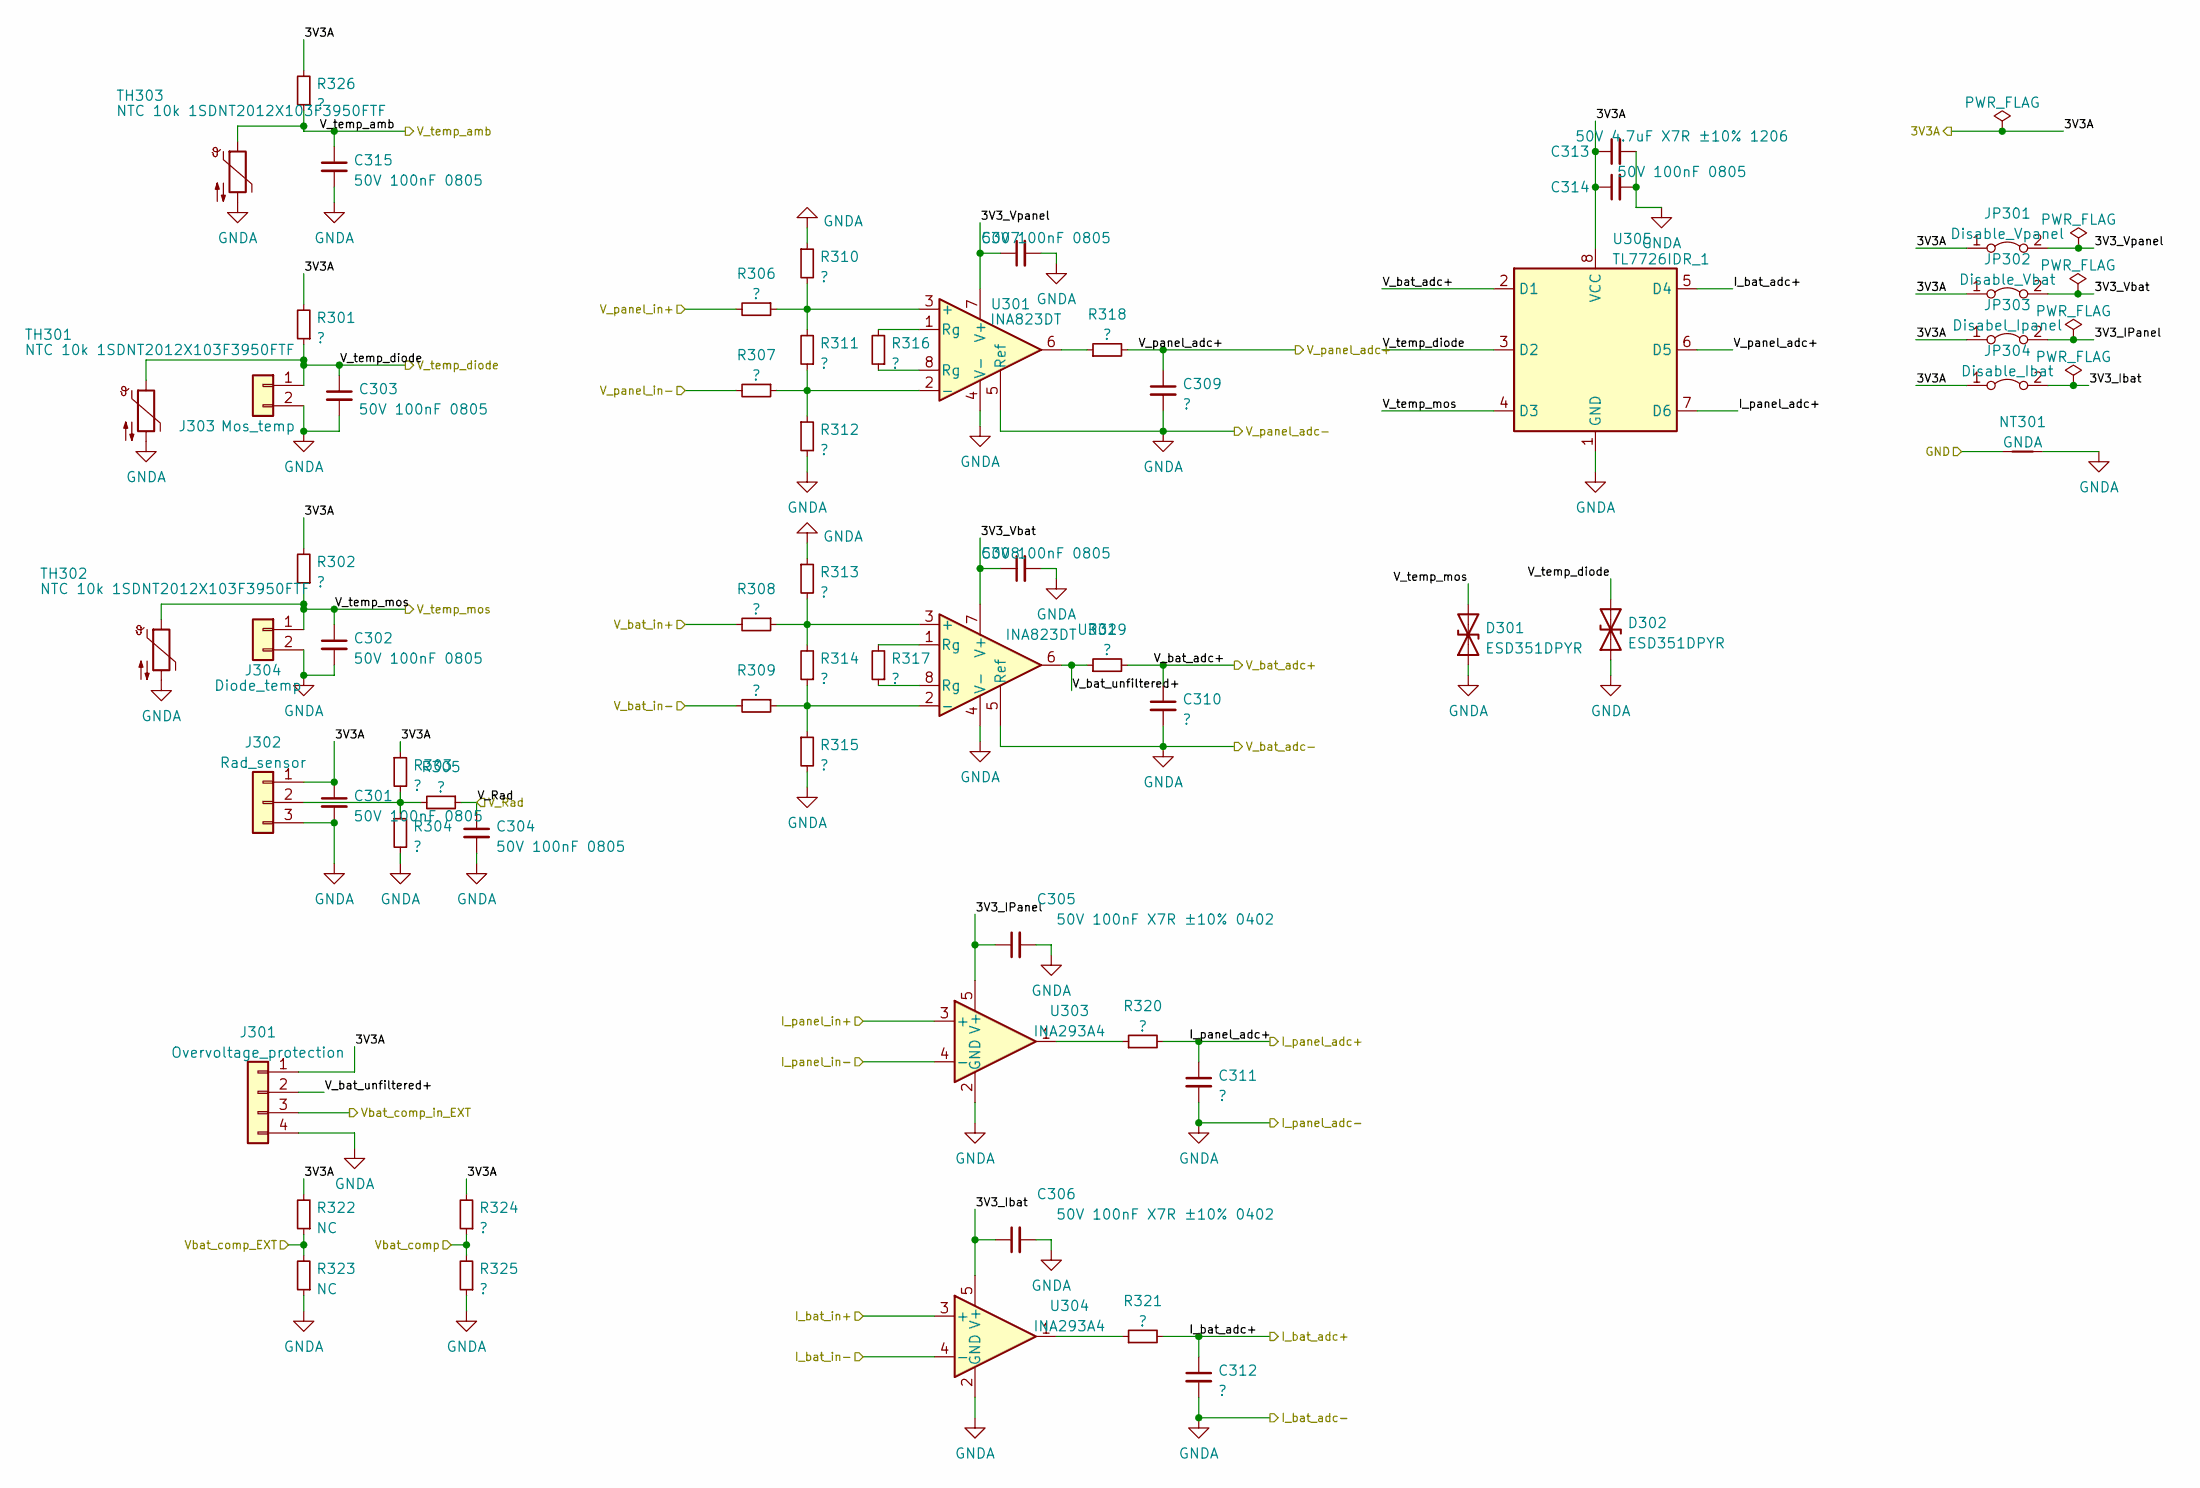
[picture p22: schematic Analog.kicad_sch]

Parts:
C301, C302, C303, C304, C307, C308, C314, C315: 50V 100nF 0805; C_0805_2012Metric_Pad1.18x1.45mm_HandSolder
C305, C306: 50V 100nF X7R ±10% 0402; C_0402_1005Metric_Pad0.74x0.62mm_HandSolder
C309, C310, C311, C312: ?; C_0805_2012Metric_Pad1.18x1.45mm_HandSolder
C313: 50V 4.7uF X7R ±10% 1206; C_1206_3216Metric_Pad1.33x1.80mm_HandSolder
D301, D302: ESD351DPYR; D_0402_1005Metric_Pad0.77x0.64mm_HandSolder
J301: Overvoltage_protection; PinHeader_1x04_P2.54mm_Vertical
J302: Rad_sensor; PinHeader_1x03_P2.54mm_Vertical
J303: Mos_temp; PinHeader_1x02_P2.54mm_Vertical
J304: Diode_temp; PinHeader_1x02_P2.54mm_Vertical
JP301: Disable_Vpanel; SolderJumper-2_P0.5mm_Open_TrianglePad0.8x0.5mm
JP302: Disable_Vbat; SolderJumper-2_P0.5mm_Open_TrianglePad0.8x0.5mm
JP303: Disabel_Ipanel; SolderJumper-2_P0.5mm_Open_TrianglePad0.8x0.5mm
JP304: Disable_Ibat; SolderJumper-2_P0.5mm_Open_TrianglePad0.8x0.5mm
NT301: GNDA; NetTie-2_SMD_Pad0.3mm
R301, R302, R303, R304, R305, R306, R307, R308, R309, R310, R311, R312, R313, R314, R315, R316, R317, R318, R319, R320, R321, R324, R325, R326: ?; R_0805_2012Metric_Pad1.20x1.40mm_HandSolder
R322, R323: NC; R_0805_2012Metric_Pad1.20x1.40mm_HandSolder
TH301, TH302, TH303: NTC 10k 1SDNT2012X103F3950FTF; R_0805_2012Metric_Pad1.20x1.40mm_HandSolder
U301, U302: INA823DT; SOIC-8_3.9x4.9mm_P1.27mm
U303, U304: INA293A4; SOT-23-5_HandSoldering
U305: TL7726IDR_1; SOIC-8_3.9x4.9mm_P1.27mm

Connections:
/3V3_Analog: C301.1, C313.1, C314.1, J301.1, J302.1, JP301.1 (A), JP302.1 (A), JP303.1 (A), JP304.1 (A), R301.2, R302.2, R303.1, R322.2, R324.2, R326.2, U305.8 (VCC); also elsewhere on the board
/Analog/3V3_IPanel: C305.1, JP303.2 (B), U303.5 (V+)
/Analog/3V3_Ibat: C306.1, JP304.2 (B), U304.5 (V+)
/Analog/3V3_Vbat: C308.1, JP302.2 (B), U302.7 (V+)
/Analog/3V3_Vpanel: C307.1, JP301.2 (B), U301.7 (V+)
/Analog/I_bat_adc+: C312.1, R321.2, U305.5 (D4); also elsewhere on the board
/Analog/I_panel_adc+: C311.1, R320.2, U305.7 (D6); also elsewhere on the board
/Analog/V_Rad: C304.1, R305.1; also elsewhere on the board
/Analog/V_bat_adc+: C310.1, R319.2, U305.2 (D1); also elsewhere on the board
/Analog/V_bat_unfiltered+: J301.2, R319.1, U302.6
/Analog/V_panel_adc+: C309.1, R318.2, U305.6 (D5); also elsewhere on the board
/Analog/V_temp_amb: C315.1, R326.1, TH303.1; also elsewhere on the board
/Analog/V_temp_diode: C303.1, D302.2 (A2), J303.1, R301.1, TH301.1, U305.3 (D2); also elsewhere on the board
/Analog/V_temp_mos: C302.1, D301.2 (A2), J304.1, R302.1, TH302.1, U305.4 (D3); also elsewhere on the board
/Analog/Vbat_comp: R324.1, R325.2; also elsewhere on the board
/Analog/Vbat_comp_EXT: R322.1, R323.2; also elsewhere on the board
/Analog/Vbat_comp_in_EXT: J301.3; also elsewhere on the board
/B+: R308.2; also elsewhere on the board
/B-: R309.2; also elsewhere on the board
/IBat+: U304.3 (+); also elsewhere on the board
/IBat-: U304.4 (-); also elsewhere on the board
/IPanel+: U303.3 (+); also elsewhere on the board
/IPanel-: U303.4 (-); also elsewhere on the board
/P+: R306.2; also elsewhere on the board
/P-: R307.2; also elsewhere on the board
GND: NT301.1; also elsewhere on the board
GNDA: C301.2, C302.2, C303.2, C304.2, C305.2, C306.2, C307.2, C308.2, C309.2, C310.2, C311.2, C312.2, C313.2, C314.2, C315.2, D301.1 (A1), D302.1 (A1), J301.4, J302.3, J303.2, J304.2, NT301.2, R304.2, R310.1, R312.2, R313.1, R315.2, R323.1, R325.1, TH301.2, TH302.2, TH303.2, U301.4 (V-), U301.5 (Ref), U302.4 (V-), U302.5 (Ref), U303.2 (GND), U304.2 (GND), U305.1 (GND); also elsewhere on the board
unnamed: J302.2, R303.2, R304.1, R305.2
unnamed: R306.1, R310.2, R311.2, U301.3 (+)
unnamed: R307.1, R311.1, R312.1, U301.2 (-)
unnamed: R308.1, R313.2, R314.2, U302.3 (+)
unnamed: R309.1, R314.1, R315.1, U302.2 (-)
unnamed: R316.1, U301.8 (Rg)
unnamed: R316.2, U301.1 (Rg)
unnamed: R317.1, U302.8 (Rg)
unnamed: R317.2, U302.1 (Rg)
unnamed: R318.1, U301.6
unnamed: R320.1, U303.1
unnamed: R321.1, U304.1

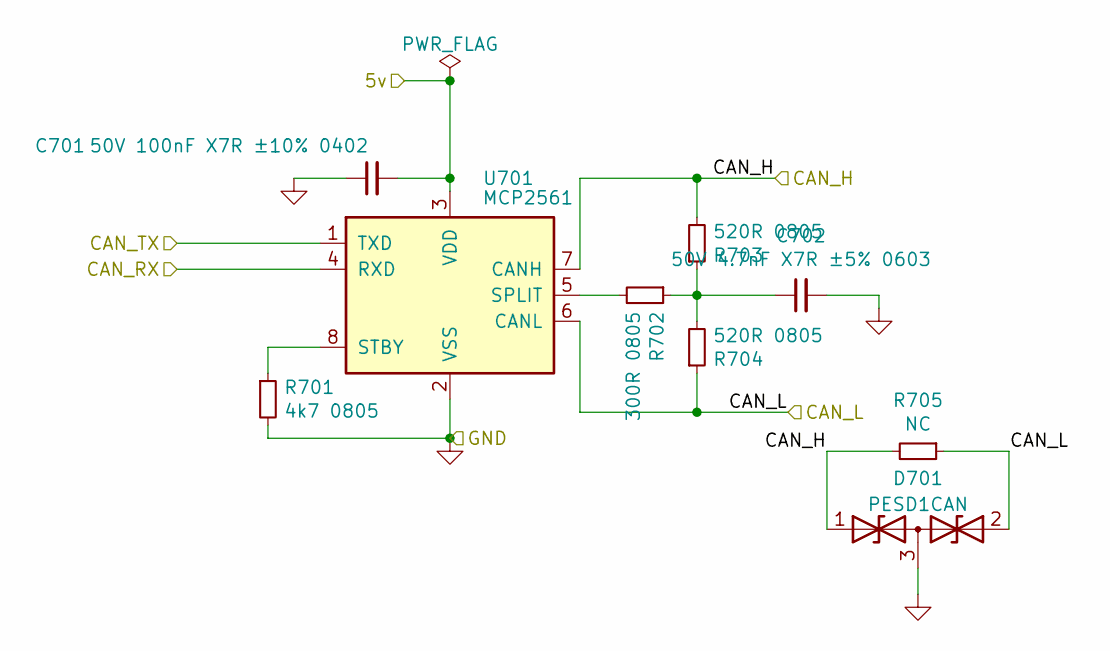
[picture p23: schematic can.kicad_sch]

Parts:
C701: 50V 100nF X7R ±10% 0402; C_0402_1005Metric_Pad0.74x0.62mm_HandSolder
C702: 50V 4.7nF X7R ±5% 0603; C_0603_1608Metric_Pad1.08x0.95mm_HandSolder
D701: PESD1CAN; SOT-23_Handsoldering
R701: 4k7 0805; R_0805_2012Metric_Pad1.20x1.40mm_HandSolder
R702: 300R 0805; R_0805_2012Metric_Pad1.20x1.40mm_HandSolder
R703, R704: 520R 0805; R_0805_2012Metric_Pad1.20x1.40mm_HandSolder
R705: NC; R_0805_2012Metric_Pad1.20x1.40mm_HandSolder
U701: MCP2561; SOIC-8_3.9x4.9mm_P1.27mm

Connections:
/5V_CAN: C701.2, U701.3 (VDD); also elsewhere on the board
/can/CAN_H: D701.1 (A1), R703.2, R705.2, U701.7 (CANH); also elsewhere on the board
/can/CAN_L: D701.2 (A2), R704.1, R705.1, U701.6 (CANL); also elsewhere on the board
/can/CAN_RX: U701.4 (RXD); also elsewhere on the board
/can/CAN_TX: U701.1 (TXD); also elsewhere on the board
GND: C701.1, C702.2, D701.3 (common), R701.2, U701.2 (VSS); also elsewhere on the board
unnamed: C702.1, R702.1, R703.1, R704.2
unnamed: R701.1, U701.8 (STBY)
unnamed: R702.2, U701.5 (SPLIT)

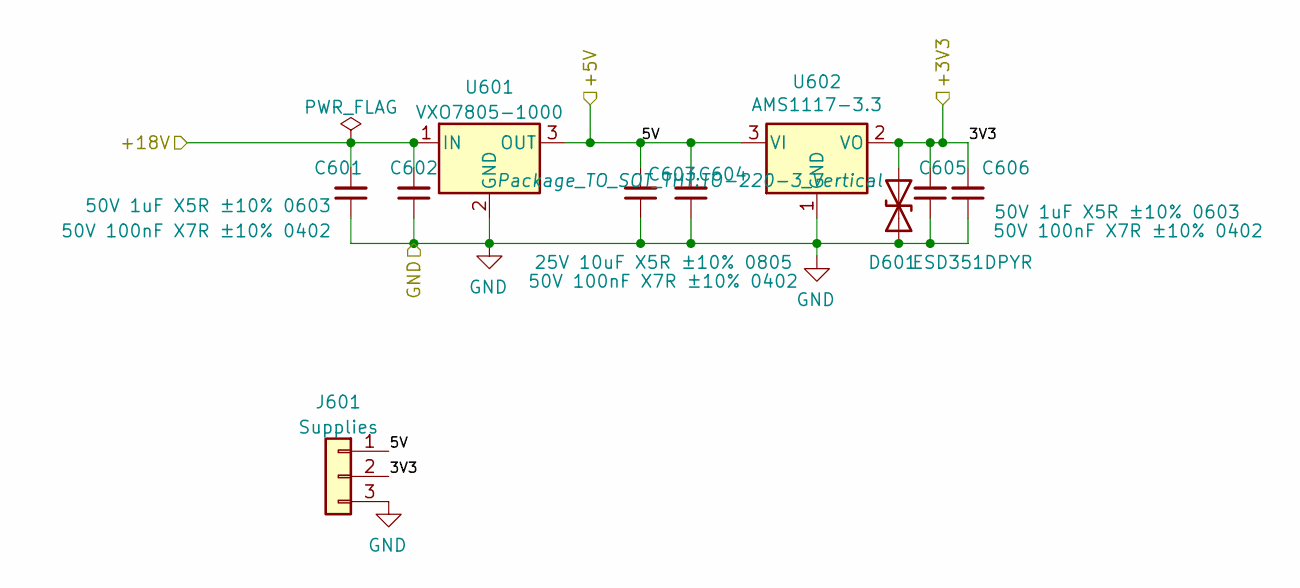
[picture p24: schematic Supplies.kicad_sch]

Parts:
C601, C606: 50V 1uF X5R ±10% 0603; C_1206_3216Metric_Pad1.33x1.80mm_HandSolder
C602, C604, C605: 50V 100nF X7R ±10% 0402; C_0603_1608Metric_Pad1.08x0.95mm_HandSolder
C603: 25V 10uF X5R ±10% 0805; C_1206_3216Metric_Pad1.33x1.80mm_HandSolder
D601: ESD351DPYR; D_0402_1005Metric_Pad0.77x0.64mm_HandSolder
J601: Supplies; PinHeader_1x03_P2.54mm_Vertical
U601: VXO7805-1000; TO-220-3_Vertical
U602: AMS1117-3.3; SOT-223-3_TabPin2

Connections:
+3V3: C605.2, C606.2, D601.2 (A2), J601.2, U602.2 (VO); also elsewhere on the board
+5V: C603.2, C604.2, J601.1, U601.3 (OUT), U602.3 (VI); also elsewhere on the board
/Supplies/+18V: C601.2, C602.2, U601.1 (IN); also elsewhere on the board
GND: C601.1, C602.1, C603.1, C604.1, C605.1, C606.1, D601.1 (A1), J601.3, U601.2 (GND), U602.1 (GND); also elsewhere on the board

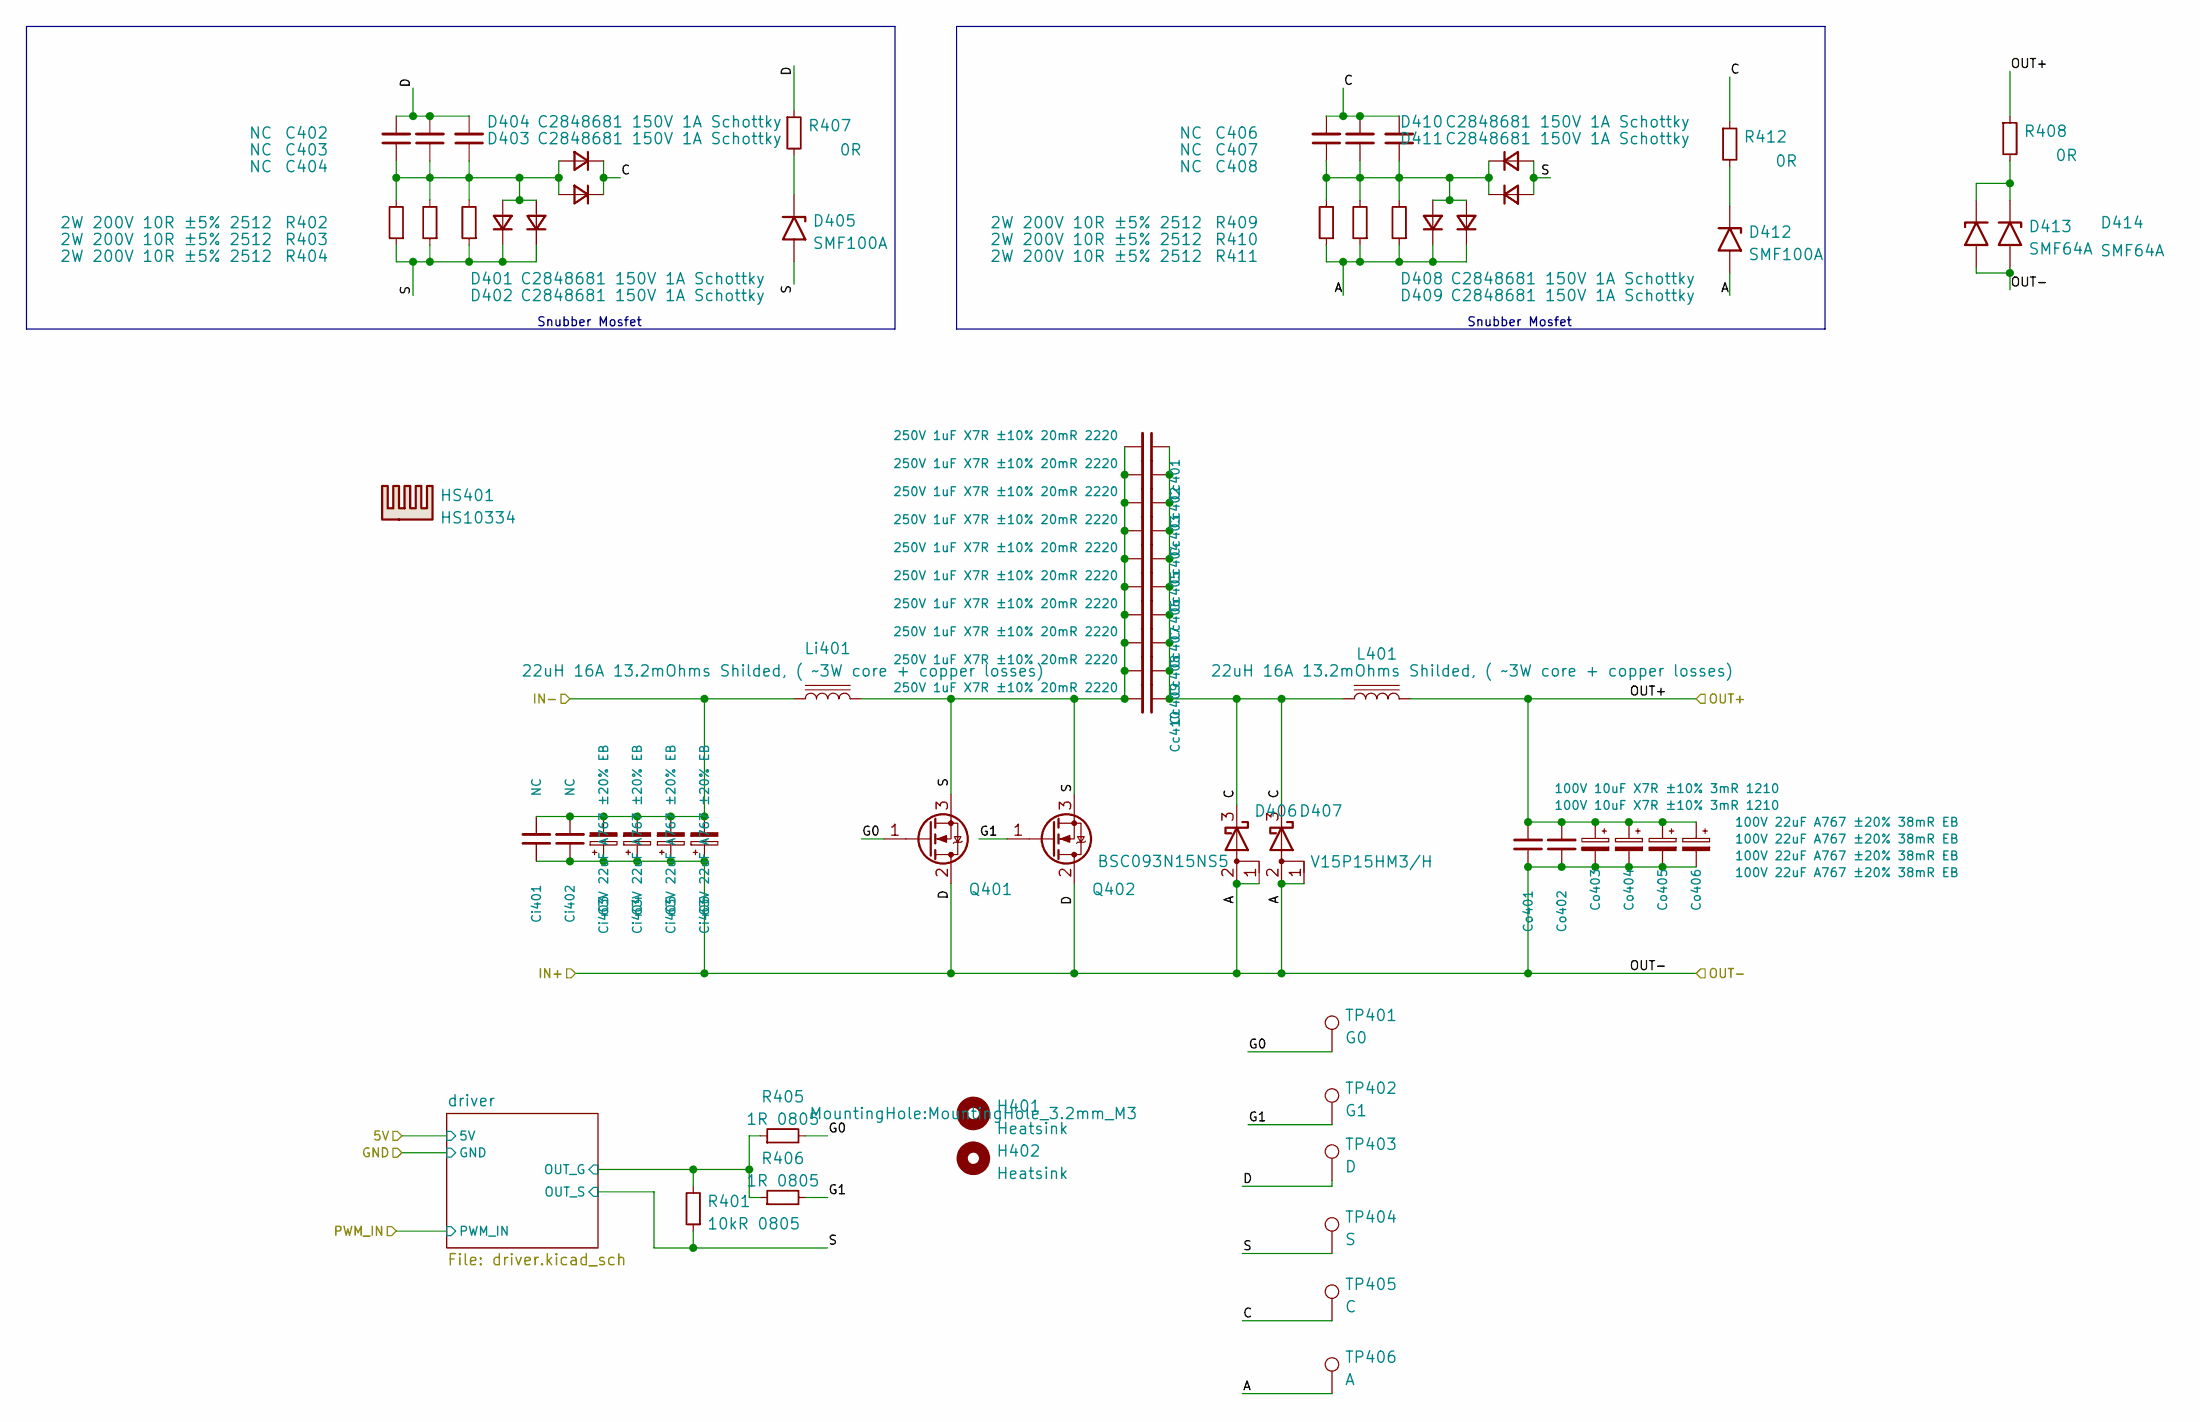
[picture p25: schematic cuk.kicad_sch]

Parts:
C402, C403, C404, C406, C407, C408: NC; C_1206_3216Metric_Pad1.33x1.80mm_HandSolder
Cc401, Cc402, Cc403, Cc404, Cc405, Cc406, Cc407, Cc408, Cc409, Cc410: 250V 1uF X7R ±10% 20mR 2220; C_2220_5650Metric
Ci401, Ci402: NC; C_1210_3225Metric
Ci403, Ci404, Ci405, Ci406: 63V 22uF A767 ±20% EB; CP_Elec_8x10
Co401, Co402: 100V 10uF X7R ±10% 3mR 1210; C_1210_3225Metric
Co403, Co404, Co405, Co406: 100V 22uF A767 ±20% 38mR EB; CP_Elec_10x12.5
D401, D402, D403, D404, D408, D409, D410, D411: C2848681 150V 1A Schottky; D_SMA
D405, D412: SMF100A; D_SOD-123F
D406, D407: V15P15HM3/H; TO-277A
D413, D414: SMF64A; D_SOD-123F
H401, H402: Heatsink; MountingHole_3.2mm_M3
HS401: HS10334; HS10334 60mmx17mm
L401: 22uH 16A 13.2mOhms Shilded, ( ~3W core + copper l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; L_Pulse_PM227
Li401: 22uH 16A 13.2mOhms Shilded, ( ~3W core + copper l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; L_Pulse_PM227
Q401, Q402: BSC093N15NS5; TDSON-8-3
R401: 10kR 0805; R_0805_2012Metric_Pad1.20x1.40mm_HandSolder
R402, R403, R404, R409, R410, R411: 2W 200V 10R ±5% 2512; R_2512_6332Metric_Pad1.40x3.35mm_HandSolder
R405, R406: 1R 0805; R_0805_2012Metric_Pad1.20x1.40mm_HandSolder
R407, R408, R412: 0R; R_0805_2012Metric_Pad1.20x1.40mm_HandSolder
TP401: G0; TestPoint_Pad_1.5x1.5mm
TP402: G1; TestPoint_Pad_1.5x1.5mm
TP403: D; TestPoint_Pad_1.5x1.5mm
TP404: S; TestPoint_Pad_1.5x1.5mm
TP405: C; TestPoint_Pad_1.5x1.5mm
TP406: A; TestPoint_Pad_1.5x1.5mm

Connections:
/B+: Co401.2, Co402.2, Co403.1, Co404.1, Co405.1, Co406.1, L401.2, R408.1; also elsewhere on the board
/Cuk/A: C402.2, C403.2, C404.2, Ci401.1, Ci402.1, Ci403.1, Ci404.1, Ci405.1, Ci406.1, Co401.1, Co402.1, Co403.2, Co404.2, Co405.2, Co406.2, D406.1 (A), D406.2 (A), D407.1 (A), D407.2 (A), D408.1 (K), D409.1 (K), D412.2 (A2), D413.2 (A2), D414.2 (A2), Q401.2 (D), Q402.2 (D), R407.1, R409.1, R410.1, R411.1, TP403.1, TP406.1; also elsewhere on the board
/Cuk/C: C406.2, C407.2, C408.2, Cc401.1, Cc402.1, Cc403.1, Cc404.1, Cc405.1, Cc406.1, Cc407.1, Cc408.1, Cc409.1, Cc410.1, D403.1 (K), D404.1 (K), D406.3 (K), D407.3 (K), L401.1, R412.1, TP405.1
/Cuk/G0: Q401.1 (G), R405.2, TP401.1
/Cuk/G1: Q402.1 (G), R406.2, TP402.1
/Cuk/S: Cc401.2, Cc402.2, Cc403.2, Cc404.2, Cc405.2, Cc406.2, Cc407.2, Cc408.2, Cc409.2, Cc410.2, D401.1 (K), D402.1 (K), D405.2 (A2), D410.2 (A), D411.2 (A), Li401.1, Q401.3 (S), Q402.3 (S), R401.1, R402.1, R403.1, R404.1, TP404.1; also elsewhere on the board
/Cuk/driver/OUT_G: R401.2, R405.1, R406.1; also elsewhere on the board
/P-: Ci401.2, Ci402.2, Ci403.2, Ci404.2, Ci405.2, Ci406.2, Li401.2; also elsewhere on the board
unnamed: C402.1, C403.1, C404.1, D401.2 (A), D402.2 (A), D403.2 (A), D404.2 (A), R402.2, R403.2, R404.2
unnamed: C406.1, C407.1, C408.1, D408.2 (A), D409.2 (A), D410.1 (K), D411.1 (K), R409.2, R410.2, R411.2
unnamed: D405.1 (A1), R407.2
unnamed: D412.1 (A1), R412.2
unnamed: D413.1 (A1), D414.1 (A1), R408.2

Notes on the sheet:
Snubber Mosfet

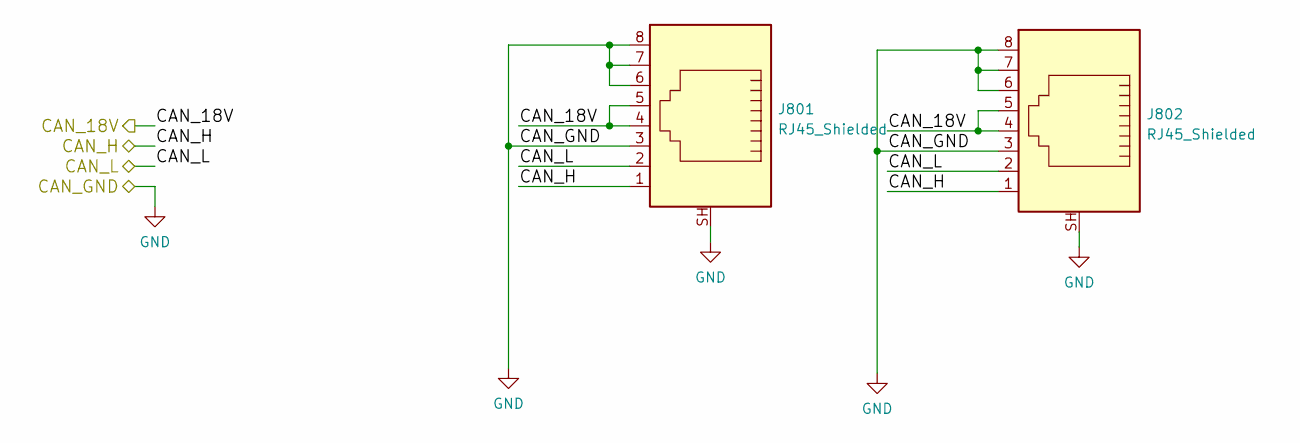
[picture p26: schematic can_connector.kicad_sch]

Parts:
J801, J802: RJ45_Shielded; RJ45_YH59_01

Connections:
/can_connector/CAN_18V: J801.4, J801.5, J802.4, J802.5; also elsewhere on the board
/can_connector/CAN_H: J801.1, J802.1; also elsewhere on the board
/can_connector/CAN_L: J801.2, J802.2; also elsewhere on the board
GND: J801.3, J801.6, J801.7, J801.8, J801.SH, J802.3, J802.6, J802.7, J802.8, J802.SH; also elsewhere on the board

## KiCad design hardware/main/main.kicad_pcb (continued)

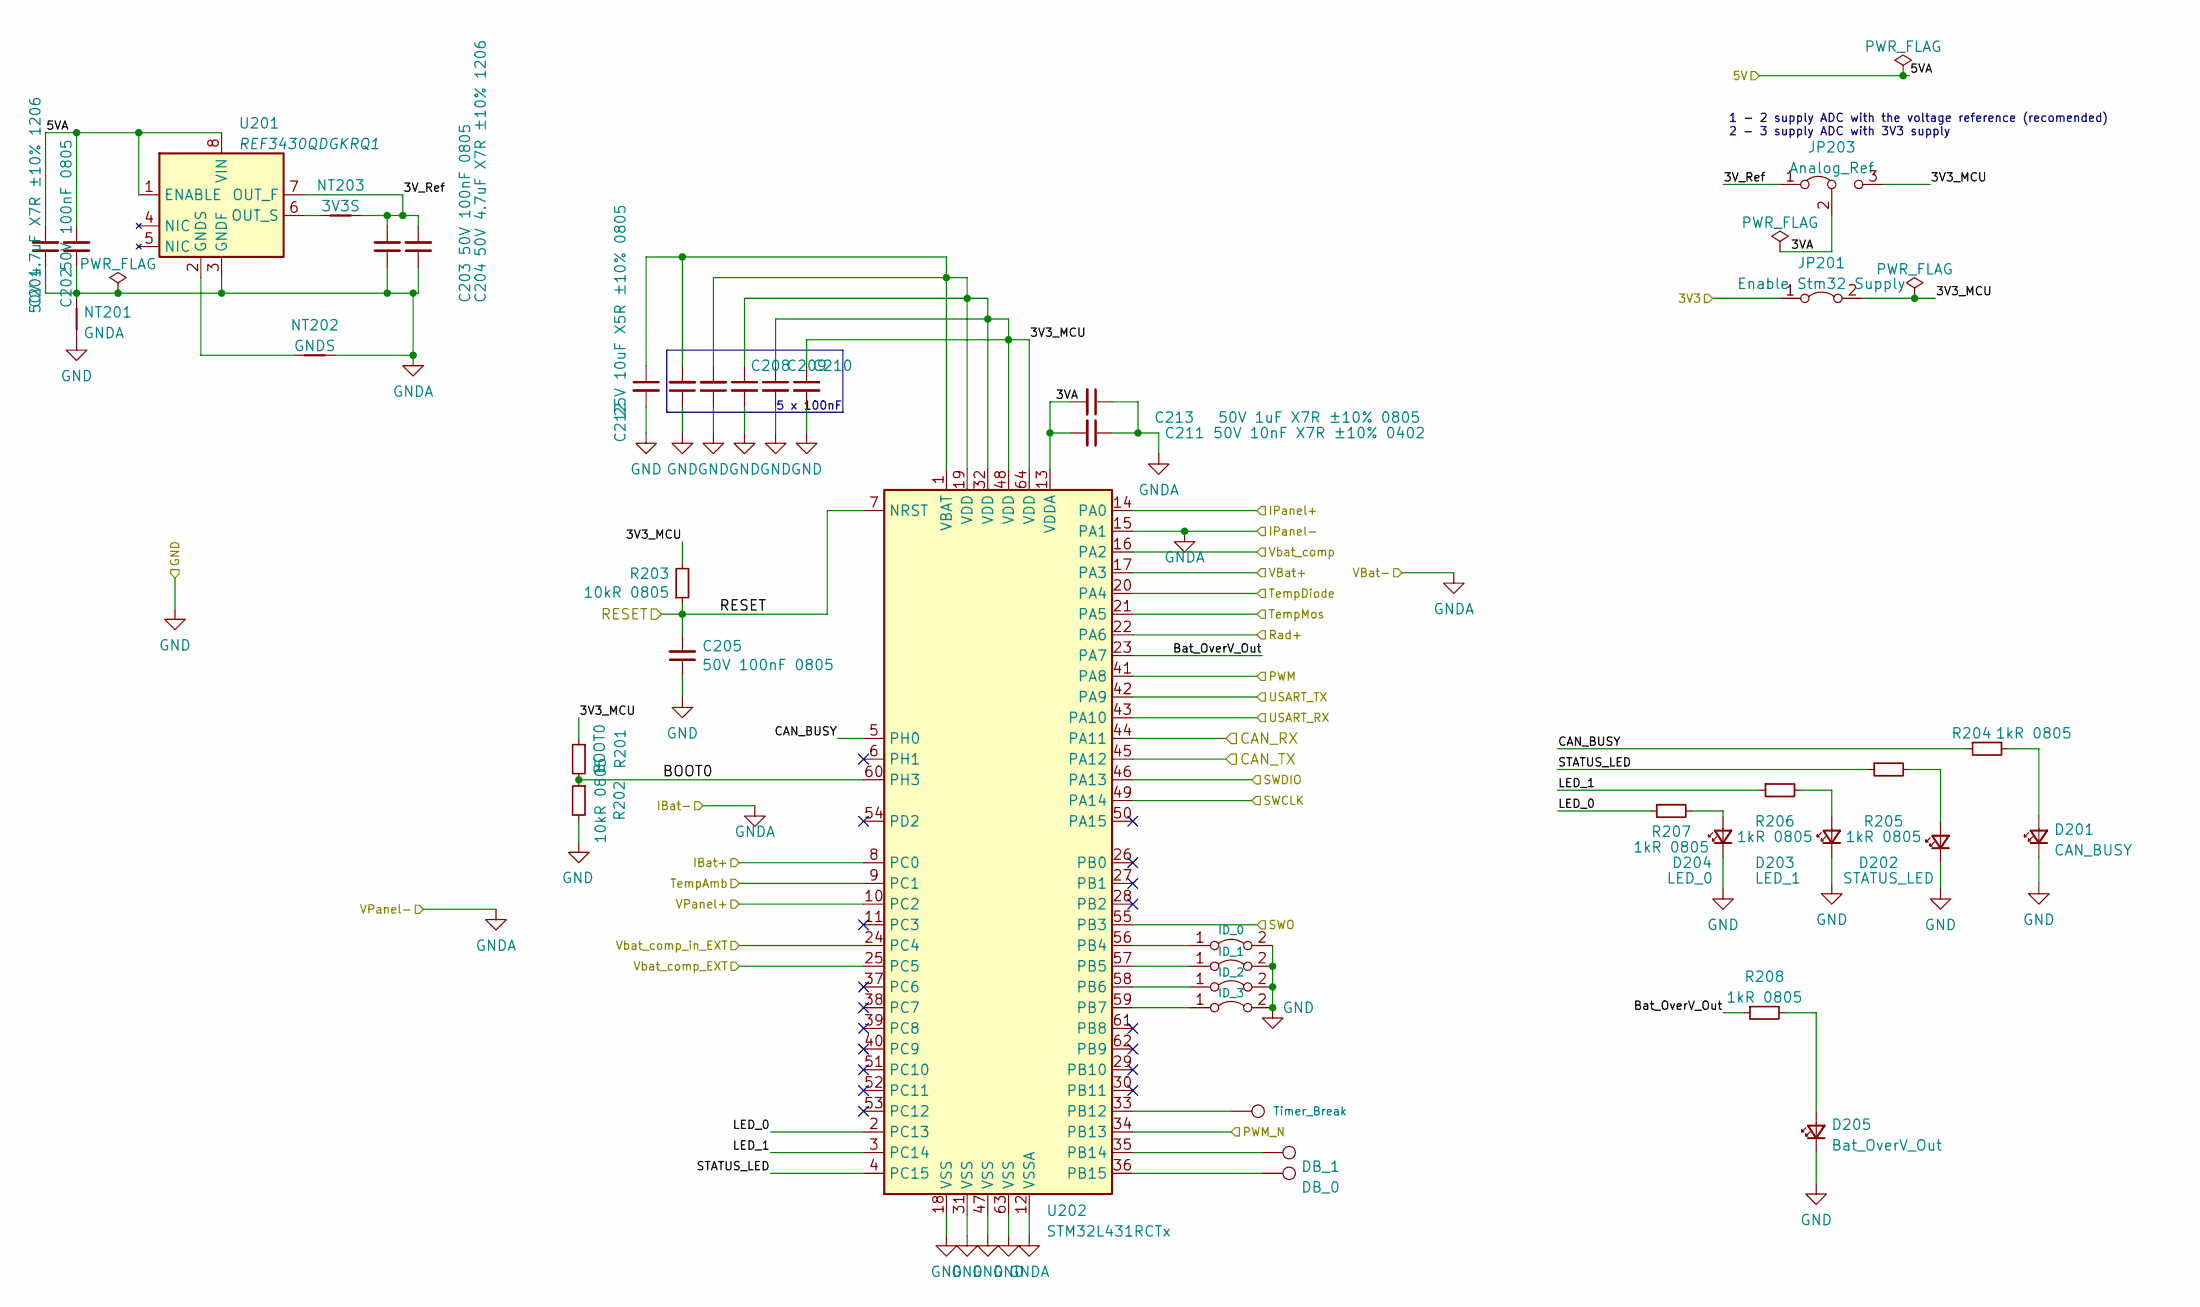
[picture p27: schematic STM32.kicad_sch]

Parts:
C201, C204: 50V 4.7uF X7R ±10% 1206; C_1206_3216Metric_Pad1.33x1.80mm_HandSolder
C202, C203, C205, C206, C207: 50V 100nF 0805; C_0805_2012Metric_Pad1.18x1.45mm_HandSolder
C208, C209, C210: 50V 100nF X7R ±10% 0402; C_0402_1005Metric_Pad0.74x0.62mm_HandSolder
C211: 50V 10nF X7R ±10% 0402; C_0402_1005Metric_Pad0.74x0.62mm_HandSolder
C212: 25V 10uF X5R ±10% 0805; C_0805_2012Metric_Pad1.18x1.45mm_HandSolder
C213: 50V 1uF X7R ±10% 0805; C_0805_2012Metric_Pad1.18x1.45mm_HandSolder
D201: CAN_BUSY; LED_0805_2012Metric_Pad1.15x1.40mm_HandSolder
D202: STATUS_LED; LED_0805_2012Metric_Pad1.15x1.40mm_HandSolder
D203: LED_1; LED_0805_2012Metric_Pad1.15x1.40mm_HandSolder
D204: LED_0; LED_0805_2012Metric_Pad1.15x1.40mm_HandSolder
D205: Bat_OverV_Out; LED_0805_2012Metric_Pad1.15x1.40mm_HandSolder
JP201: Enable Stm32 Supply; SolderJumper-2_P0.5mm_Open_TrianglePad0.8x0.5mm
JP203: Analog_Ref; SolderJumper-3_P0.5mm_Open_TrianglePad0.8x0.5mm
JP204: ID_0; SolderJumper-2_P0.5mm_Open_TrianglePad0.8x0.5mm
JP205: ID_1; SolderJumper-2_P0.5mm_Open_TrianglePad0.8x0.5mm
JP206: ID_2; SolderJumper-2_P0.5mm_Open_TrianglePad0.8x0.5mm
JP207: ID_3; SolderJumper-2_P0.5mm_Open_TrianglePad0.8x0.5mm
NT201: GNDA; NetTie-2_SMD_Pad0.3mm
NT202: GNDS; NetTie-2_SMD_Pad0.3mm
NT203: 3V3S; NetTie-2_SMD_Pad0.3mm
R201: BOOT0; R_0402_1005Metric
R202, R203: 10kR 0805; R_0805_2012Metric_Pad1.20x1.40mm_HandSolder
R204, R205, R206, R207, R208: 1kR 0805; R_0805_2012Metric_Pad1.20x1.40mm_HandSolder
TP201: DB_0; TestPoint_Pad_1.0x1.0mm_small
TP202: DB_1; TestPoint_Pad_1.0x1.0mm_small
TP203: Timer_Break; TestPoint_Pad_1.0x1.0mm_small
U201: REF3430QDGKRQ1; VSSOP-8_3.0x3.0mm_P0.65mm
U202: STM32L431RCTx; LQFP-64_10x10mm_P0.5mm

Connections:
/3V3_STM: JP201.1 (A); also elsewhere on the board
/5V_STM: C201.2, C202.2, U201.1 (ENABLE), U201.8 (VIN); also elsewhere on the board
/Analog/I_bat_adc+: U202.8 (PC0); also elsewhere on the board
/Analog/I_panel_adc+: U202.14 (PA0); also elsewhere on the board
/Analog/V_Rad: U202.22 (PA6); also elsewhere on the board
/Analog/V_bat_adc+: U202.17 (PA3); also elsewhere on the board
/Analog/V_panel_adc+: U202.10 (PC2); also elsewhere on the board
/Analog/V_temp_amb: U202.9 (PC1); also elsewhere on the board
/Analog/V_temp_diode: U202.20 (PA4); also elsewhere on the board
/Analog/V_temp_mos: U202.21 (PA5); also elsewhere on the board
/Analog/Vbat_comp: U202.16 (PA2); also elsewhere on the board
/Analog/Vbat_comp_EXT: U202.25 (PC5); also elsewhere on the board
/Analog/Vbat_comp_in_EXT: U202.24 (PC4); also elsewhere on the board
/PWM: U202.41 (PA8); also elsewhere on the board
/RESET: C205.2, R203.1, U202.7 (NRST); also elsewhere on the board
/STM32/3V3_MCU: C206.2, C207.2, C208.1, C209.1, C210.1, C212.1, JP201.2 (B), JP203.3 (B), R201.1, R203.2, U202.1 (VBAT), U202.19 (VDD), U202.32 (VDD), U202.48 (VDD), U202.64 (VDD)
/STM32/3VA: C211.2, C213.2, JP203.2 (C), U202.13 (VDDA)
/STM32/3V_Ref: C203.2, C204.2, JP203.1 (A), NT203.1, U201.7 (OUT_F)
/STM32/BOOT0: R201.2, R202.1, U202.60 (PH3)
/STM32/Bat_OverV_Out: R208.1, U202.23 (PA7)
/STM32/CAN_BUSY: R204.1, U202.5 (PH0)
/STM32/CAN_RX: U202.44 (PA11); also elsewhere on the board
/STM32/CAN_TX: U202.45 (PA12); also elsewhere on the board
/STM32/LED_0: R207.1, U202.2 (PC13)
/STM32/LED_1: R206.1, U202.3 (PC14)
/STM32/PWM_N: U202.34 (PB13)
/STM32/STATUS_LED: R205.1, U202.4 (PC15)
/SWCLK: U202.49 (PA14); also elsewhere on the board
/SWDIO: U202.46 (PA13); also elsewhere on the board
/SWO: U202.55 (PB3); also elsewhere on the board
/USART_RX: U202.43 (PA10); also elsewhere on the board
/USART_TX: U202.42 (PA9); also elsewhere on the board
GND: C205.1, C206.1, C207.1, C208.2, C209.2, C210.2, C212.2, D201.1 (K), D202.1 (K), D203.1 (K), D204.1 (K), D205.1 (K), JP204.2 (B), JP205.2 (B), JP206.2 (B), JP207.2 (B), NT201.2, R202.2, U202.18 (VSS), U202.31 (VSS), U202.47 (VSS), U202.63 (VSS); also elsewhere on the board
GNDA: C201.1, C202.1, C203.1, C204.1, C211.1, C213.1, NT201.1, NT202.1, U201.3 (GNDF), U202.12 (VSSA), U202.15 (PA1); also elsewhere on the board
unnamed: D201.2 (A), R204.2
unnamed: D202.2 (A), R205.2
unnamed: D203.2 (A), R206.2
unnamed: D204.2 (A), R207.2
unnamed: D205.2 (A), R208.2
unnamed: JP204.1 (A), U202.56 (PB4)
unnamed: JP205.1 (A), U202.57 (PB5)
unnamed: JP206.1 (A), U202.58 (PB6)
unnamed: JP207.1 (A), U202.59 (PB7)
unnamed: NT202.2, U201.2 (GNDS)
unnamed: NT203.2, U201.6 (OUT_S)
unnamed: TP201.1, U202.36 (PB15)
unnamed: TP202.1, U202.35 (PB14)
unnamed: TP203.1, U202.33 (PB12)

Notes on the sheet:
1 - 2 supply ADC with the voltage reference (recomended) 2 - 3 supply ADC with 3V3 supply
5 x 100nF

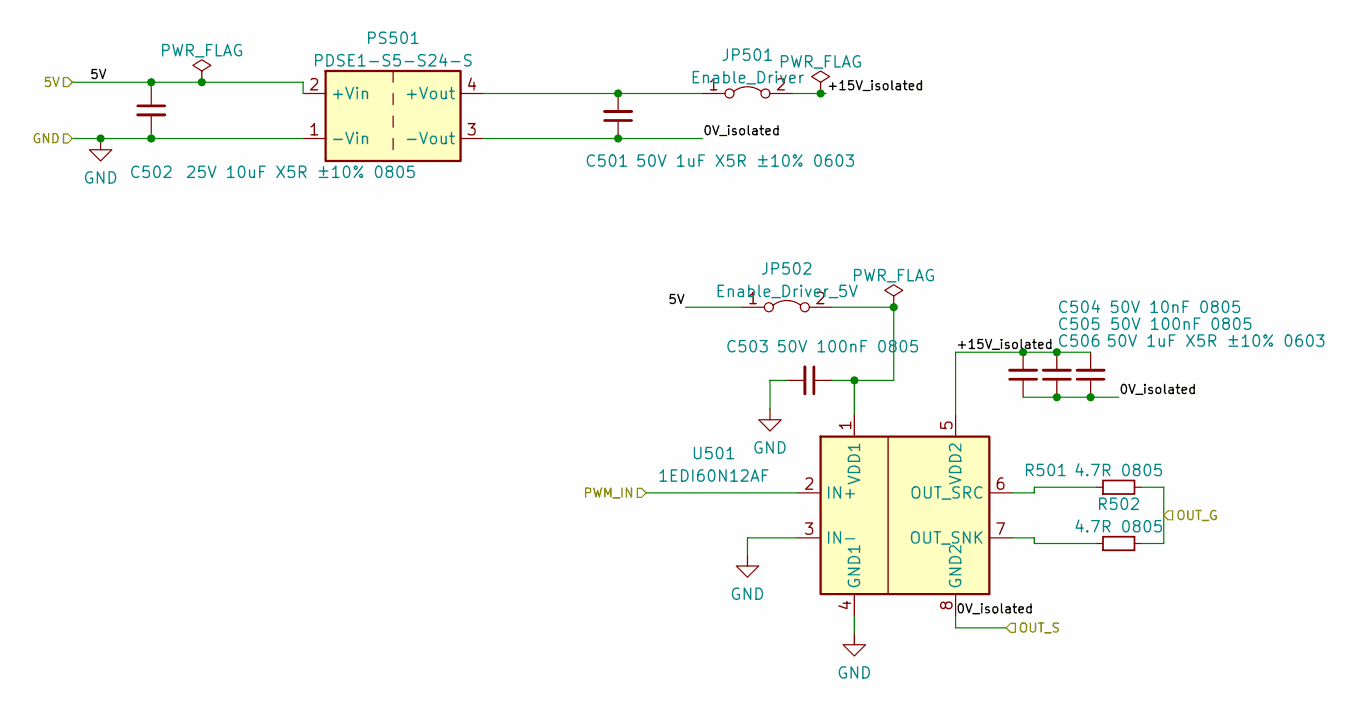
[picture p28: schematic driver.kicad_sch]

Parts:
C501, C506: 50V 1uF X5R ±10% 0603; C_0603_1608Metric_Pad1.08x0.95mm_HandSolder
C502: 25V 10uF X5R ±10% 0805; C_0805_2012Metric_Pad1.18x1.45mm_HandSolder
C503, C505: 50V 100nF 0805; C_0805_2012Metric_Pad1.18x1.45mm_HandSolder
C504: 50V 10nF 0805; C_0805_2012Metric_Pad1.18x1.45mm_HandSolder
JP501: Enable_Driver; SolderJumper-2_P0.5mm_Open_TrianglePad0.8x0.5mm
JP502: Enable_Driver_5V; SolderJumper-2_P0.5mm_Open_TrianglePad0.8x0.5mm
PS501: PDSE1-S5-S24-S; Converter_DCDC_Murata_MEE3SxxxxSC_THT
R501, R502: 4.7R 0805; R_0805_2012Metric_Pad1.20x1.40mm_HandSolder
U501: 1EDI60N12AF; SOIC-8_3.9x4.9mm_P1.27mm

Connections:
/5V_Driver: C502.1, JP502.1 (A), PS501.2 (+Vin); also elsewhere on the board
/Cuk/PWM_IN: U501.2 (IN+); also elsewhere on the board
/Cuk/S: C501.1, C504.1, C505.1, C506.1, PS501.3 (-Vout), U501.8 (GND2); also elsewhere on the board
/Cuk/driver/+15V_isolated: C504.2, C505.2, C506.2, JP501.2 (B), U501.5 (VDD2)
/Cuk/driver/OUT_G: R501.2, R502.2; also elsewhere on the board
GND: C502.2, C503.2, PS501.1 (-Vin), U501.3 (IN-), U501.4 (GND1); also elsewhere on the board
unnamed: C501.2, JP501.1 (A), PS501.4 (+Vout)
unnamed: C503.1, JP502.2 (B), U501.1 (VDD1)
unnamed: R501.1, U501.6 (OUT_SRC)
unnamed: R502.1, U501.7 (OUT_SNK)

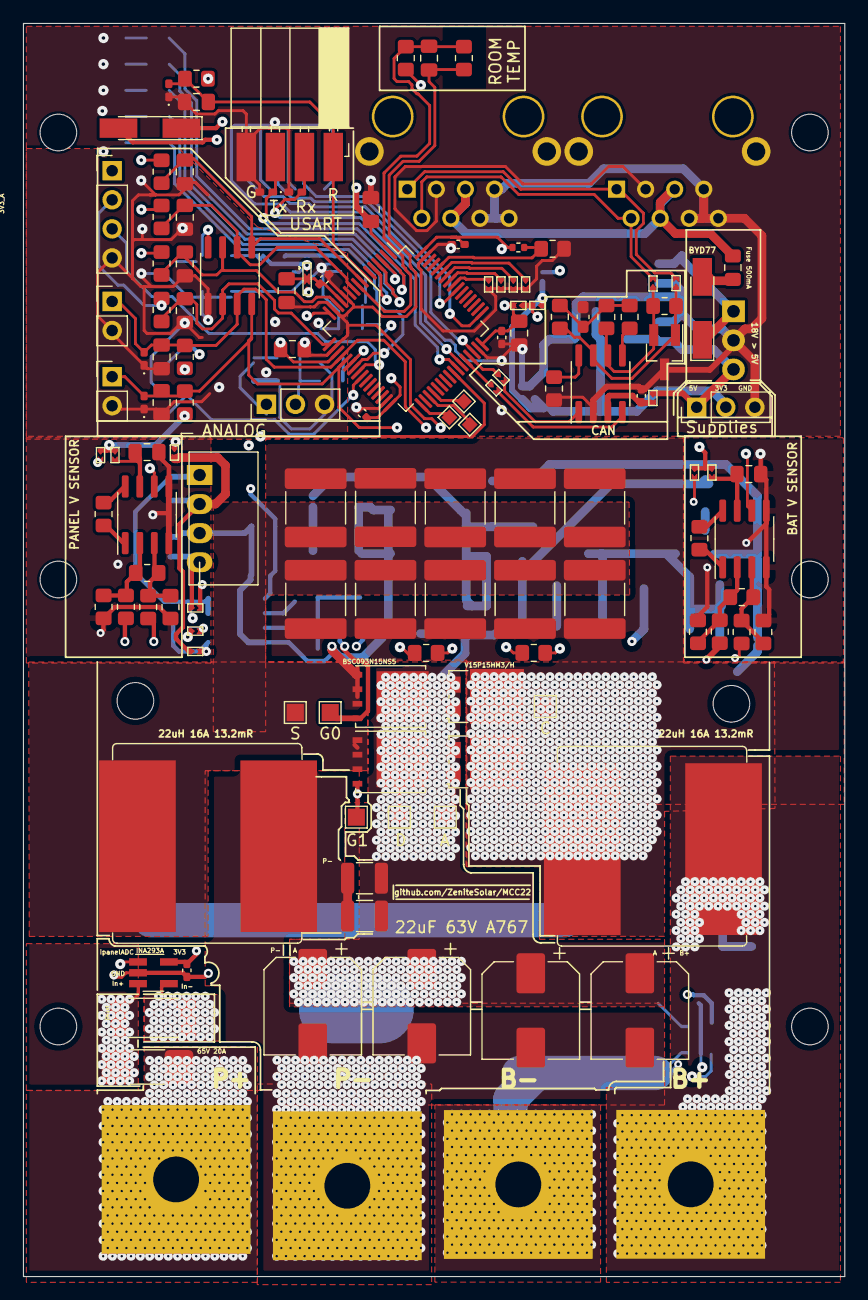
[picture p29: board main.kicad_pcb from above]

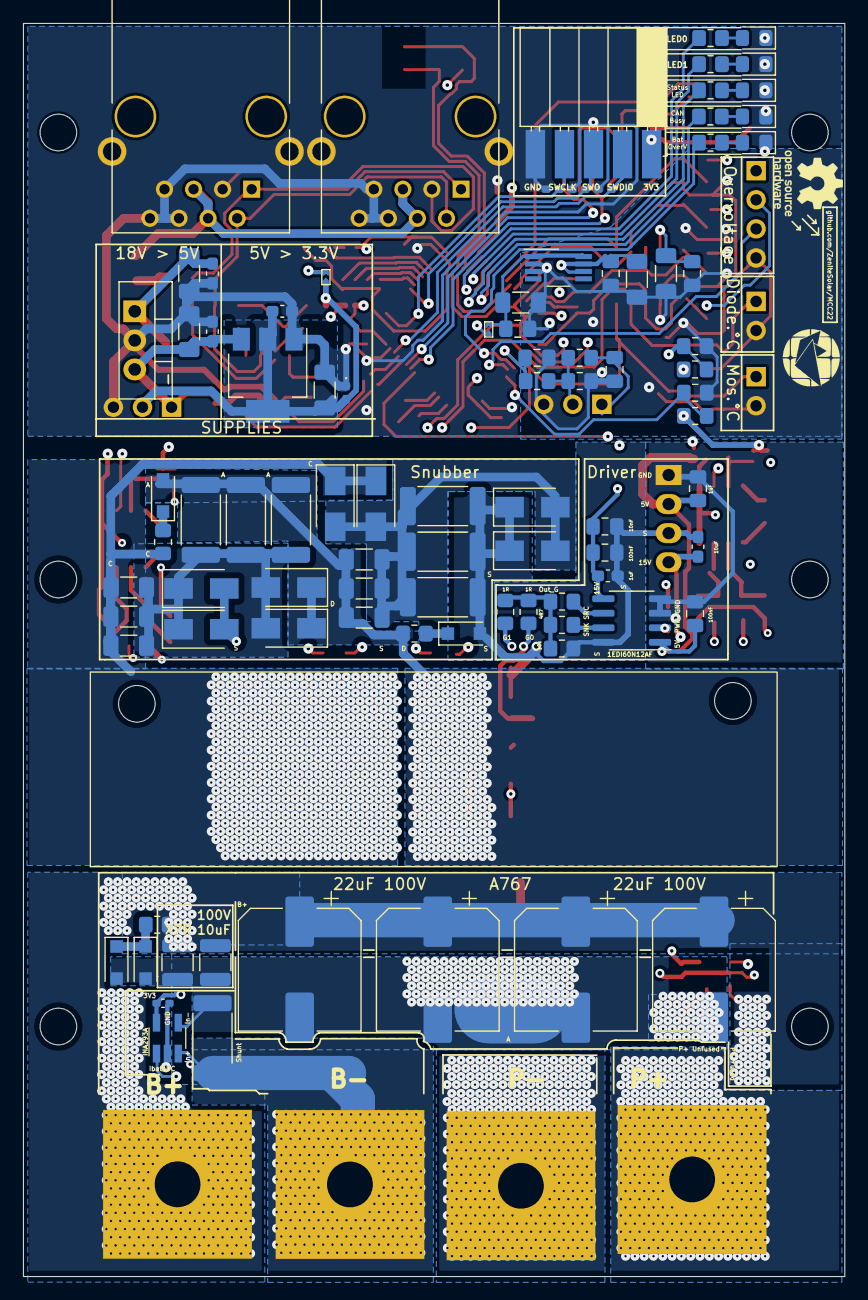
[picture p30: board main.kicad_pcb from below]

Board: 4 copper layers, 71.8 x 109.5 mm, 237 parts (100 on the bottom side), 108 nets.

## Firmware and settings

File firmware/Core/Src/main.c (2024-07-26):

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
/* Includes ------------------------------------------------------------------*/
#include "main.h"

/* USER CODE BEGIN Includes */
#include <string.h>
#include "machine.h"
#include "control.h"
#include "comparators.h"
#include "pwm.h"
#include "adc.h"
#include "canbus.h"
#include "dac.h"
#include "uart.h"
#include "ads111x.h"

/* USER CODE END Includes */

ADC_HandleTypeDef hadc1;
DMA_HandleTypeDef hdma_adc1;

CAN_HandleTypeDef hcan1;

COMP_HandleTypeDef hcomp1;
COMP_HandleTypeDef hcomp2;

DAC_HandleTypeDef hdac1;

I2C_HandleTypeDef hi2c3;
DMA_HandleTypeDef hdma_i2c3_rx;

IWDG_HandleTypeDef hiwdg;

TIM_HandleTypeDef htim1;
TIM_HandleTypeDef htim2;

UART_HandleTypeDef huart1;
DMA_HandleTypeDef hdma_usart1_rx;

void SystemClock_Config(void);
static void MX_GPIO_Init(void);
static void MX_DMA_Init(void);
static void MX_ADC1_Init(void);
static void MX_CAN1_Init(void);
static void MX_TIM1_Init(void);
static void MX_USART1_UART_Init(void);
static void MX_COMP1_Init(void);
static void MX_COMP2_Init(void);
static void MX_DAC1_Init(void);
static void MX_TIM2_Init(void);
static void MX_I2C3_Init(void);
static void MX_IWDG_Init(void);
/**
	* @brief  The application entry point.
	* @retval int
	*/
int main(void)
{

	/* MCU Configuration--------------------------------------------------------*/

	/* Reset of all peripherals, Initializes the Flash interface and the Systick. */
	HAL_Init();

	/* Configure the system clock */
	SystemClock_Config();

	/* Initialize all configured peripherals */
	MX_GPIO_Init();
	MX_DMA_Init();
	MX_ADC1_Init();
	MX_CAN1_Init();
	MX_TIM1_Init();
	MX_USART1_UART_Init();
	MX_COMP1_Init();
	MX_COMP2_Init();
	MX_DAC1_Init();
	MX_TIM2_Init();
	MX_I2C3_Init();
	MX_IWDG_Init();
	/* USER CODE BEGIN 2 */

	uart_init(&huart1);
	adc_init(&hi2c3);
	pwm_init(&htim1);
	machine_init();
	canbus_init(&hcan1);
	
	/* USER CODE END 2 */

	/* Infinite loop */
	/* USER CODE BEGIN WHILE */
	while (1)
	{
		/* USER CODE END WHILE */

		/* USER CODE BEGIN 3 */

		static uint32_t uart_delay = 0U;
		static uint32_t adc_delay = 0U;
		static uint32_t control_delay = 0U;
		static uint32_t canbus_delay = 0U;

		/* Machine */
		machine_set_run();
		machine_set_enable(DISABLE);
		machine_run();

		/* Uart */
		if (uart_delay < HAL_GetTick())
		{
			uart_delay = HAL_GetTick() + 500U;
			uart_run();
		}

		/* Adc */
		if (adc_delay < HAL_GetTick())
		{
			adc_delay = HAL_GetTick() + (uint32_t)(1000 / ADC_DEFAULT_FREQUENCY);
			adc_measure();
		}

		/* Control */
		if (control_delay < HAL_GetTick() && adc_all_channels_measured())
		{
			control_delay = HAL_GetTick() + control_get_period();
			control_run();
		}

		/* CanBus */
		if (canbus_delay < HAL_GetTick())
		{
			canbus_delay = HAL_GetTick() + 50U;
			canbus_run();
		}

	}
	/* USER CODE END 3 */
}

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
/* USER CODE BEGIN 4 */
void HAL_TIM_PeriodElapsedCallback(TIM_HandleTypeDef *htim)
{
	if (htim == &htim2)
	{
		HAL_GPIO_TogglePin(DB_1_GPIO_Port, DB_1_Pin);
	}
}

/* USER CODE END 4 */
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


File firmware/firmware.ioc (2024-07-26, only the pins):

Mcu.UserName=STM32L431RCTx
PA0.GPIO_Label=IPanel+
PA0.Signal=ADCx_IN5
PA10.Signal=USART1_RX
PA11.Signal=CAN1_RX
PA12.Signal=CAN1_TX
PA2.GPIO_Label=Vbat_comp
PA2.Signal=SharedAnalog_PA2
PA3.GPIO_Label=Vbat+
PA3.Signal=SharedAnalog_PA3
PA4.GPIO_Label=TempDiode
PA4.Signal=ADCx_IN9
PA5.GPIO_Label=TempMos
PA5.Signal=ADCx_IN10
PA6.GPIO_Label=Rad+
PA6.Signal=ADCx_IN11
PA7.GPIO_Label=Bat_OverV_Out
PA7.Signal=COMP2_OUT
PA8.GPIO_Label=PWM
PA8.Signal=S_TIM1_CH1
PA9.Signal=USART1_TX
PB0.GPIO_Label=Bat_OverV_Out_EXT
PB0.Signal=COMP1_OUT
PB12.GPIO_Label=TImer_break
PB12.Signal=TIM1_BKIN_COMP2
PB13.GPIO_Label=PWM_N
PB13.Signal=TIM1_CH1N
PB14.GPIO_Label=DB_1
PB14.Signal=GPIO_Output
PB15.GPIO_Label=DB_0
PB15.Signal=GPIO_Output
PB5.GPIO_Label=ID_1
PB5.Signal=GPIO_Input
PB6.GPIO_Label=ID_2
PB6.Signal=GPIO_Input
PB7.GPIO_Label=ID_3
PB7.Signal=GPIO_Input
PC0.GPIO_Label=ADC_SCL
PC0.Signal=I2C3_SCL
PC1.GPIO_Label=ADC_SDA
PC1.Signal=I2C3_SDA
PC13.GPIO_Label=LED_0
PC13.Signal=GPIO_Output
PC2.GPIO_Label=Vpanel+
PC2.Signal=ADCx_IN3
PC4.GPIO_Label=Vbat_comp_in_EXT
PC4.Signal=COMP1_INM
PC5.GPIO_Label=Vbat_comp_EXT
PC5.Signal=SharedAnalog_PC5

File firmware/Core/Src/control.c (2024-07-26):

#include "control.h"
#include "peo.h"
#include "brute_force.h"
#include "fixed.h"
#include "pi.h"
#include "peo_dynamic_step.h"

/**
 * @brief Enable/disable control variables print
 * 
 */
uint8_t print;

/**
 * @brief Control main structure
 * 
 */
static control_t control;

/**
 * @brief initialize control variables
 */
void control_init(void);

/**
 * @brief control start script
 */
void control_start(void);

/**
 * @brief enable/disable control,
 * set duty cycle to 0 if disabled
 * start control if enabled
 */
void control_set_enable(FunctionalState enable);

void control_init(void)
{
	print = 1;

	if (pwm_start(DEFAULT_PWM_FREQUENCY, PWM_MIN) != HAL_OK)
	{
		LOG_ERROR("error starting pwm");
	}

	control_set_freq(CONTROL_DEFAULT_FREQUENCY);
	control_start();
}

void control_set_error(errors_t error)
{
	control.errors = error;
}

/**
 * @brief  Set control period
 * 
 * @param period control period in ms
 */
void control_set_period(uint32_t period)
{
	if (period < (uint32_t)(1000 / ADC_DEFAULT_FREQUENCY))
	{
		LOG_ERROR("control period can't be faster than adc period, setting to adc period");
		control.period = (uint32_t)(1000 / ADC_DEFAULT_FREQUENCY);
		return;
	}

	control.period = period;
}

/**
 * @brief Get control period
 * 
 * @return uint32_t control period in ms
 */
uint32_t control_get_period(void)
{
	return control.period;
}

/**
 * @brief Set control frequency
 * 
 * @param freq control frequency in Hz
 */
void control_set_freq(float freq)
{
	control_set_period((uint32_t)(1000 / freq));
}

/**
 * @brief Get control frequency
 * 
 * @return float control frequency in Hz
 */
float control_get_freq(void)
{
	return 1 / control.period;
}

void control_set_print(uint8_t enable)
{
	print = enable;
}

/**
 * Control algorithms transitions
 */
void control_set_brute_force(float initial_duty)
{
	brute_force_init(initial_duty);
	control.algorithm_running = BRUTE_FORCE;
}

void control_set_peo(float initial_duty)
{
	peo_init(initial_duty);
	control.algorithm_running = PEO;
}

void control_set_peo_dynamic_step(float initial_duty)
{
	peo_dynamic_step_init(initial_duty);
	control.algorithm_running = PEO_DYN_STEP;
}

void control_set_pi(float initial_duty)
{
	pi_init(initial_duty);
	control.algorithm_running = PI;
}

void control_set_fixed(float initial_duty)
{
	fixed_init(initial_duty);
	control.algorithm_running = FIXED;
}


void control_start(void)
{
	control.forced_algorithm = DISABLE;
	control.errors = 0;
	control_set_brute_force(0.6);
}

void control_set_enable(FunctionalState enable)
{
	control.enable = enable;
	if (enable == DISABLE)
		control_set_fixed(0.0);
	else
		control_start();
}

algorithms_t control_get_algorithm(void)
{
	return control.algorithm_running;
}

errors_t control_get_error_state(void)
{
	return control.errors;
}

void control_force_algorithm(algorithms_t algorithm, float initial_duty)
{

	switch (algorithm)
	{
	case BRUTE_FORCE:
		control_set_brute_force(initial_duty);
		break;
	case PEO:
		control_set_peo(initial_duty);
		break;
	case PEO_DYN_STEP:
		control_set_peo_dynamic_step(initial_duty);
		break;
	case PI:
		control_set_pi(initial_duty);
		break;
	case FIXED:
		control_set_fixed(initial_duty);
		break;
	default:
		return;
	}

	control.forced_algorithm = ENABLE;
}

/**
 * @brief Script for the control logic,
 * this function describes the sequence and the conditions to use different algorithms
 */
void control_script(void)
{
	static uint32_t error_triggered_time = 0;
	static float max_power = 0.0;

	/* Save maximum power */
	if (max_power < adc_get_value(ADC_PANEL_VOLTAGE) * adc_get_value(ADC_PANEL_CURRENT))
	{
		max_power = adc_get_value(ADC_PANEL_VOLTAGE) * adc_get_value(ADC_PANEL_CURRENT);
	}

	if (adc_get_value(ADC_BATTERY_VOLTAGE) > CONTROL_MAXIMUM_BATTERY_VOLTAGE)
	{
		control.errors |= OUTPUT_OVER_VOLTAGE;
	}

	if (control.errors && !error_triggered_time){
		/* Error handling */
		control_set_fixed(0.0);
		printf("Trating errors\n");
		error_triggered_time = HAL_GetTick();
	}

	/* Wait CONTROL_ERROR_RESET_MILLIS when a error was triggered for system stabilization*/
	if (error_triggered_time)
	{
		if ((error_triggered_time + CONTROL_ERROR_RESET_MILLIS > HAL_GetTick()))
		{
			//control_set_fixed(0.0);
			printf("Waiting system stabilization\n");
			return;
		} else
		{
			control.errors = 0;
			error_triggered_time = 0;
			control_set_brute_force(0.1);
			return;
		}
	}

	if (control.forced_algorithm)
		return;

	// When brute force ends initialize the continuous algorithm
	if (control.algorithm_running == BRUTE_FORCE && brute_force_get_metadata()->done)
	{
		control_set_peo(brute_force_get_metadata()->absolute_mpp_duty);
	}

	//if power is too low, maybe the algorithm is lost or power reduced from maximum
	static uint32_t last_brute_force_time = 0;
	float panel_power = adc_get_value(ADC_PANEL_VOLTAGE) * adc_get_value(ADC_PANEL_CURRENT);
	uint8_t power_too_low = panel_power <= MINIMUM_POWER;
	uint8_t power_reduced = panel_power < (max_power * 0.8);
	if ( 
		(power_too_low || power_reduced) && 
		(control.algorithm_running != BRUTE_FORCE)
	)
	{
		if (HAL_GetTick() >= last_brute_force_time)
		{
			max_power = 0.0;
			last_brute_force_time = HAL_GetTick() + 10000;
			printf("Power too low, running brute force from algorithm %d\n", control.algorithm_running);
			control_set_brute_force(0.2f);
			return;
		}
	}

}

void control_run(void)
{
	static float duty = PWM_MIN;
	static uint32_t print_delay = 0;

	/* Compute adc average */
	adc_calculate_average();

	/* Control algorithms decision script */
	control_script();

	switch (control.algorithm_running)
	{
	case BRUTE_FORCE:
		duty = brute_force_run();
		break;
	case PEO:
		duty = peo_run();
		break;
	case PEO_DYN_STEP:
		duty = peo_dynamic_step_run();
		break;
	case PI:
		duty = pi_run();
		break;
	case FIXED:
		duty = fixed_run();
		break;
	default:
		control_set_brute_force(0.0);
		duty = 0;
	}

	if (print)
	{
		if (print_delay < HAL_GetTick())
		{
			print_delay = HAL_GetTick() + 500;
			printf("Algo: %d, Vpan: %0.2f, Ipan: %0.2f, Vbat: %0.2f, Ibat: %0.2f, Duty: %0.2f, Freq: %0.1f, Pin: %0.2f, Pout: %0.2f, Eff: %0.2f\n", 
				control.algorithm_running,
				adc_get_value(ADC_PANEL_VOLTAGE),
				adc_get_value(ADC_PANEL_CURRENT),
				adc_get_value(ADC_BATTERY_VOLTAGE),
				adc_get_value(ADC_BATTERY_CURRENT),
				pwm_get_duty() * 100.0f,
				pwm_get_freq(),
				adc_get_value(ADC_PANEL_VOLTAGE) * adc_get_value(ADC_PANEL_CURRENT),
				adc_get_value(ADC_BATTERY_VOLTAGE) * adc_get_value(ADC_BATTERY_CURRENT),
				(adc_get_value(ADC_BATTERY_VOLTAGE) * adc_get_value(ADC_BATTERY_CURRENT)) / (adc_get_value(ADC_PANEL_VOLTAGE) * adc_get_value(ADC_PANEL_CURRENT)) * 100.0f
			);
		}
	}

	pwm_set_duty(duty);

}

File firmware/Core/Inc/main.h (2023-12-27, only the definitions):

#define LED_0_Pin GPIO_PIN_13
#define LED_0_GPIO_Port GPIOC
#define LED_1_Pin GPIO_PIN_14
#define LED_1_GPIO_Port GPIOC
#define LED_STATUS_Pin GPIO_PIN_15
#define LED_STATUS_GPIO_Port GPIOC
#define LED_CAN_BUSY_Pin GPIO_PIN_0
#define LED_CAN_BUSY_GPIO_Port GPIOH
#define ADC_SCL_Pin GPIO_PIN_0
#define ADC_SCL_GPIO_Port GPIOC
#define ADC_SDA_Pin GPIO_PIN_1
#define ADC_SDA_GPIO_Port GPIOC
#define Vpanel__Pin GPIO_PIN_2
#define Vpanel__GPIO_Port GPIOC
#define IPanel__Pin GPIO_PIN_0
#define IPanel__GPIO_Port GPIOA
#define Vbat_comp_Pin GPIO_PIN_2
#define Vbat_comp_GPIO_Port GPIOA
#define Vbat__Pin GPIO_PIN_3
#define Vbat__GPIO_Port GPIOA
#define TempDiode_Pin GPIO_PIN_4
#define TempDiode_GPIO_Port GPIOA
#define TempMos_Pin GPIO_PIN_5
#define TempMos_GPIO_Port GPIOA
#define Rad__Pin GPIO_PIN_6
#define Rad__GPIO_Port GPIOA
#define Bat_OverV_Out_Pin GPIO_PIN_7
#define Bat_OverV_Out_GPIO_Port GPIOA
#define Vbat_comp_in_EXT_Pin GPIO_PIN_4
#define Vbat_comp_in_EXT_GPIO_Port GPIOC
#define Vbat_comp_EXT_Pin GPIO_PIN_5
#define Vbat_comp_EXT_GPIO_Port GPIOC
#define Bat_OverV_Out_EXT_Pin GPIO_PIN_0
#define Bat_OverV_Out_EXT_GPIO_Port GPIOB
#define TImer_break_Pin GPIO_PIN_12
#define TImer_break_GPIO_Port GPIOB
#define PWM_N_Pin GPIO_PIN_13
#define PWM_N_GPIO_Port GPIOB
#define DB_1_Pin GPIO_PIN_14
#define DB_1_GPIO_Port GPIOB
#define DB_0_Pin GPIO_PIN_15
#define DB_0_GPIO_Port GPIOB
#define PWM_Pin GPIO_PIN_8
#define PWM_GPIO_Port GPIOA
#define ID_0_Pin GPIO_PIN_4
#define ID_0_GPIO_Port GPIOB
#define ID_1_Pin GPIO_PIN_5
#define ID_1_GPIO_Port GPIOB
#define ID_2_Pin GPIO_PIN_6
#define ID_2_GPIO_Port GPIOB
#define ID_3_Pin GPIO_PIN_7
#define ID_3_GPIO_Port GPIOB

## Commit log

2022-10-31 Schematics: create schematics of STM32, cuk converter, canbus, analog interface
    [Analog.kicad_sch, STM32.kicad_sch, Snubber.kicad_sch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]
2022-11-01 Schematics: finalize Analog Snubber and Supplies
    [Analog.kicad_sch, STM32.kicad_sch, Supplies.kicad_sch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]
2022-11-01 Schematics: Modified component values
    [Analog.kicad_sch, STM32.kicad_sch, can.kicad_sch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]
2022-11-01 Schematics: Sym table and libs updated
    [Analog.kicad_sch, STM32.kicad_sch, can_connector.kicad_sch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]
2022-11-01 Simulation: Simulating snubber with crossing diode
2022-11-01 Firmware: config stm32 pinout
2022-11-03 Schematics: Run DRC and fix errors and some warnings, also added Zenite kicad library repo as submodule
    [Analog.kicad_sch, STM32.kicad_sch, Supplies.kicad_sch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]
2022-11-03 gitignore: add kicad backup files
2022-11-04 Layout: Organizing components
    [Analog.kicad_sch, Supplies.kicad_sch, cuk.kicad_sch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]
2022-11-06 Add optimization analysis with LTSPICE non ideal components.
    [2_optimizing_components_dataset_mean.csv]
2022-11-07 Layout: Organizing power components
    [Analog.kicad_sch, STM32.kicad_sch, Supplies.kicad_sch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]
2022-11-07 Firmware: add comparator inputs in Batery Voltage and CAN Signature selector inputs
2022-11-07 Schematics: Add STM32 comparator for Battery OverVoltage
    [Analog.kicad_sch, STM32.kicad_sch, Supplies.kicad_sch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]
2022-11-10 Layout: Fist version of power stage
    [Analog.kicad_sch, STM32.kicad_sch, cuk.kicad_sch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]
2022-11-10 Layout: oganizing components of Driver and voltage sensors
    [main.kicad_pcb]
2022-11-11 Layout: Organize and initialize routing of control
    [Analog.kicad_sch, STM32.kicad_sch, cuk.kicad_sch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]
2022-11-12 Schematics: Anotate testpoints
    [cuk.kicad_sch, main.kicad_sch]
2022-11-12 Layout: Control stage routing
    [main.kicad_pcb]
2022-11-13 Schematics: Switch 2 Clamp inputs for better routing
    [Analog.kicad_sch]
2022-11-13 Schematics: Change LED order for better pcb routing
    [STM32.kicad_sch]
2022-11-13 Layout: Nearly complete control stage routing
    [main.kicad_pcb]
2022-11-14 Layout: WIP updating control
    [STM32.kicad_sch, Supplies.kicad_sch, can.kicad_sch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]
2022-11-15 Layout: Designing thermal dissipation and optimizing control
    [Analog.kicad_sch, STM32.kicad_sch, cuk.kicad_sch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]
2022-11-15 Lib: Update ZeniteKicadLib to use Heatsink and solder jumper
2022-11-15 Layout: Connect all unconected nets, and fix all DRC errors
    [Analog.kicad_sch, STM32.kicad_sch, cuk.kicad_sch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]
2022-11-15 Layout: Create Copper zone under NTC temperature sensor for a better thermal coupling
    [main.kicad_pcb]
2022-11-20 Layout: Silkscreen updated
    [main.kicad_pcb, main.kicad_sch]
2022-11-20 layout: Separating analogical power nets
    [Analog.kicad_sch, STM32.kicad_sch, Supplies.kicad_sch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]
2022-11-20 Layout: Place components and route analog, supplies and CAN
    [Analog.kicad_sch, STM32.kicad_sch, Supplies.kicad_sch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]
2022-11-22 Layout: Finalize first vesion of control (DRC ok) and modify vias for better via density
    [Analog.kicad_sch, STM32.kicad_sch, can.kicad_sch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]
2022-11-22 Layout: create margin for mechanical fixation
    [main.kicad_pcb]
2022-11-24 Layout: Update silkscreen
    [main.kicad_pcb]
2022-11-24 layout: fix path of heatsink (using relative path)
    [main.kicad_pcb]
2022-11-24 Fix size of isolated DC/DC converter
    [main.kicad_pcb]
2022-11-24 Change board surface finish to HAL SnPb
    [main.kicad_pcb]
2022-11-26 WIP: adding more compact vias
    [main-B_Cu.gbr, main-B_Mask.gbr, main-B_Paste.gbr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]
2022-11-27 Layout: Fix DRC issues, fix some copper zones, copy silkscreen of 5f991268df1bec187c9dadc35024444e2526c1c0
2022-11-27 Better GNDA + silk work
    [Analog.kicad_sch, main.kicad_sch]
2022-11-27 Fix some vias, export schematic pdf and pcb gerbers
    [main-B_Cu.gbl, main-B_Cu.gbr, main-B_Mask.gbr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]
2022-12-09 Notebook for calculation of ADC timings, results implemented in Cube
2022-12-09 verify if is not necessary shift over sample result
2023-03-12 Firmware: Implement some mppt algorithms PeO: perturb and observe Pi: is in Work in Porgress Fixed: simple constant pwm Brute_force: iterate over all pwm possibilities with a constant step
    [brute_force.c, fixed.c, peo.c]
2023-03-12 Firmware: Implement some utils, like usart debugging information and leds utils
2023-03-12 Firmware: Implement pwm functions like init, set frequency and duty, and get frequency and duty
2023-03-12 Firmware: Implement adc average using DMA, adc initilizer and adc linearization
2023-03-12 Firmware: export uart handler for logging prints
2023-03-12 Firmware: Implement comparator for battery overvoltage protection
2023-03-17 add hardware interactive BOM
2023-03-20 add BOM in markdown
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2023-03-23 initialize pwm and adc
2023-03-23 add uart callbacks and DMA
2023-03-25 Update main and code generator to use UART
2023-03-25 create uart parser similiar to SCPI
2023-03-25 add uart commands to get and set control algorithms
2023-03-25 Update documentation of the uart adding control algorithms commands
2023-04-20 change adc frequency via uart
2023-07-25 improve control script trating errors and added control variables print
    [conf.h, control.c, control.h]
2023-07-25 feat[UART] added reset and all measurements command
    [uart.c]
2023-07-25 feat[ADC] improve adc linearization and convert adc temperature values to Celsius
2023-07-25 feat[ADC]: added function to get the adc frequency
2023-07-25 fix[constants]: fixx some constants
    [conf.h]
2023-07-25 cleaning[adc]: cleaned identation in the adc file
2023-07-25 feat[LEDS]: Added animation to show the signature number when initialize the board
2023-07-25 fix[protections]: increase DAC voltage to increase the trigger voltage of the OVP
    [main.c]
2023-07-25 fix[timming]: fix uart delay
    [main.c]
2023-07-25 doc[test]: added how to test the board after solder
2023-07-25 design[adc]: added adc linearization jupyter
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2023-07-25 fix[identation]: convert identation to tabs and fix some warnings
    [adc.c, comparators.c, control.c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]
2023-07-30 add sweep and fix constants of peo
    [conf.h, control.c, peo.c]
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2023-12-27 feat[adc]: configure extern adc with ads111x on stmcubemx
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2023-12-27 feat[log] fixed log macro to accept multiple parameters like printf
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2023-12-27 feat[adc]: Refactor adc file to use a extern adc
2023-12-27 feat[adc]: Refactor control and algorithms files to use extern adc
2023-12-27 feat[adc]: fix some files to be compatible with new adc
    [control.c, control.h, main.c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]
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2023-12-27 fix[adc]: fixed some non void functions returning void
    [adc.c, control.c]
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2024-02-26 tests: tested different frequencies to get optimum PWM frequency
2024-02-26 freat: added overvoltage error handling
    [control.c]
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2024-02-26 fix(main): added missing semi colon
    [main.c]
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2024-05-01 fix(canbus): saving canbus handler instead of pointer of it
    [canbus.c, main.c]
2024-05-01 fix(canbus): missing schedule next message after send message
    [canbus.c]
2024-05-01 fix(canbus): fix board number calculation was inverting the signature
    [machine.c, utils.c]
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2024-05-01 feat(canbus): updated mcc ids and messages from mcc19 to mcc23
2024-05-01 remove .lck kicad files and add it on gitignore
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2024-07-16 feat(canbus): handle error when sending message
    [canbus.c]
2024-07-16 fix: check if mailbox have space for next message
    [canbus.c]
2024-07-26 feat: added whatchdog and check if power reduced

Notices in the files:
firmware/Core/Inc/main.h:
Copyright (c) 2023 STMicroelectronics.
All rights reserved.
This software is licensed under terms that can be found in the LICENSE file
